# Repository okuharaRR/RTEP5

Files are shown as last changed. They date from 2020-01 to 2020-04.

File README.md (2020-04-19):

<p align="center">
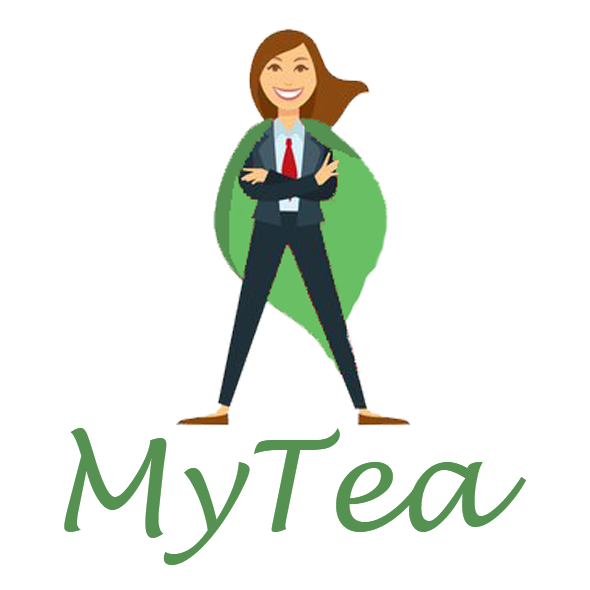
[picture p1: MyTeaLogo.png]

</p>

# MyTea - The perfect cuppa, every time

Welcome to the MyTea github page - the tea making machine which brings you the perfect tea experience!

_A Raspberry PI will be used to control the entire process of tea preparation. Depending on the tea chosen by the user, the system will heat up water to the required temperature, dispense the required amount of tea leaves into a filter, infuse the leaves for a specified time, and finally pour the tea into a cup._

_With so many coffee machines available to satisfy every variety of coffee that anyone has ever came up with, this product aims to deliver the ultimate tea experience in an office environment or a public institution so that tea drinkers are not left at the mercy of the primitive old kettle..._

## Installation

On the terminal of a Raspberry Pi type the following:

```git clone https://github.com/okuharaRR/RTEP5.git```

```cd TeaMaker```

```qmake```

```make```

```./TeaMaker```

[Qt](https://www.qt.io/download) and [WiringPi](http://wiringpi.com/) are required.

If ```make``` gives an error, try ```make clean``` first and ```make```.

## Using the application

Once a finished product is made, using it will be straightforward:

1. Fill up the kettle with water and make sure the switch in the back is in the ON position. (_The need for a mechanical switch is for user safety_.)
2. Fill up the dispenser with tea leaves.
3. Once done, turn on the RPI and launch the GUI application.
4. Follow the guide [here](https://github.com/okuharaRR/RTEP5/wiki/User-Manual).

That's it!

## Demonstration

_Covid-19 has caused a significant distruption of our project and a complete demonstartor cannot be built to date. More information about the impact of the outbreak can be found [here](https://github.com/okuharaRR/RTEP5/wiki/Impact-of-Covid-19)._

A demonstration of the current state of the project can be found [here](https://www.youtube.com/watch?v=PhV0StMdRJc).

## Team Structure
* Boris Yanchev
   * hardware design, implementation and testing
   * mechanical design, procurement and manufacturing
   * GUI conceptual design
   * marketing
* Mika Okuhara
   * software development and documentation
   * hardware and software integration
   * test GUI implementation
* Muhammad Adeel Akram
   * marketing

## Further links

For further information about our project, have a look at our [Wiki](https://github.com/okuharaRR/RTEP5/wiki).

For software documentation, please click [here](https://okuhararr.github.io/RTEP5/).

You can find our website [here](https://rtesps.wixsite.com/mytea). 

Also, be sure to like our [Facebook page](https://www.facebook.com/MyTea-%E8%8C%B6-114110590136382/) and follow our [Twitter](https://twitter.com/MyTea76121892) to get all the latest updates!

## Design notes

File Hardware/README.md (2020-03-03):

*** RTEP5 MyTea Hardware ReadMe File ***

Each subfolder contains the layout masks, schematics, and BOMs for each PCB used in the project.

The layout masks can be used directly for PCB fabrication. 

The interactive BOMs, when opened with an internet browser, can be used to see individual component placement and track the population of components.

Similarly, the text BOMs show all components used in text form.

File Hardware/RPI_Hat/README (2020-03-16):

This folder contains the KiCad files for the PI hat for connections to the rest of the sub-modules.

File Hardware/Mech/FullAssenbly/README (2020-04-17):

This folder contains the SOLIDWORKS models for the complete assembly.

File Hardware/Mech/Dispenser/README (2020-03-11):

SOLIDWORKS models for the tea dispenser can be found here.

Prototype dispenser built using 3mm laser-cut perspex sheets.

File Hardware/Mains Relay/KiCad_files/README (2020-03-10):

KiCad files for the sub-module are included here.

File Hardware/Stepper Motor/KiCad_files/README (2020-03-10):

KiCad files for the stepper motor sub-module can be found here.

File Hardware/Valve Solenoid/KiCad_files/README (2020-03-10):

KiCad files for the solenoid valve sub-module can be found here.

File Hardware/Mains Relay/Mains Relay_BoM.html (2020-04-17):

# C:\Users\Boris\Documents\KiCad Projects\RTEP5\Mains Relay\Mains Relay.sch

12.4.2020 г. 17:43:26

Eeschema (5.0.2)-1

Component Count:9

Ref | Qnty | Value | Part | Datasheet | Description | Vendor
C1 | 1 | 0.01u | Device:C | ~ | Unpolarized capacitor
D1 | 1 | Q_TRIAC_A1A2G | Device:Q_TRIAC_A1A2G | ~ | Triode for alternating current, anode1/anode2/gate
HS1 | 1 | Heatsink | Mechanical:Heatsink | | Heatsink
J1 | 1 | Conn_01x02_Male | Connector:Conn_01x02_Male | ~ | Generic connector, single row, 01x02, script generated (kicad-library-utils/schlib/autogen/connector/)
R2 | 1 | 120 | Device:R | ~ | Resistor
R3 | 1 | 360 | Device:R | ~ | Resistor
R4 | 1 | 330 | Device:R | ~ | Resistor
R5 | 1 | 39 | Device:R | ~ | Resistor
U1 | 1 | MOC3061M | Relay_SolidState:MOC3061M | http://www.fairchildsemi.com/ds/MO/MOC3061M.pdf | Zero Cross Opto-Triac, Vdrm 600V, Ift 15mA, DIP6

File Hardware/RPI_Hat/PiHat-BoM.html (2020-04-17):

# C:\Users\Boris\Documents\KiCad Projects\RTEP5\PiHat\PiHat.sch

12.4.2020 г. 18:15:18

Eeschema (5.0.2)-1

Component Count:9

Ref | Qnty | Value | Part | Datasheet | Description | Vendor
D1, D2 | 2 | LED | Device:LED | ~ | Light emitting diode
J1, J4 | 2 | Conn_01x03 | Connector_Generic:Conn_01x03 | ~ | Generic connector, single row, 01x03, script generated (kicad-library-utils/schlib/autogen/connector/)
J2 | 1 | Conn_01x04 | Connector_Generic:Conn_01x04 | ~ | Generic connector, single row, 01x04, script generated (kicad-library-utils/schlib/autogen/connector/)
J3 | 1 | Conn_02x20_Odd_Even | Connector_Generic:Conn_02x20_Odd_Even | ~ | Generic connector, double row, 02x20, odd/even pin numbering scheme (row 1 odd numbers, row 2 even numbers), script generated (kicad-library-utils/schlib/autogen/connector/)
J5 | 1 | Conn_01x02 | Connector_Generic:Conn_01x02 | ~ | Generic connector, single row, 01x02, script generated (kicad-library-utils/schlib/autogen/connector/)
R1, R2 | 2 | R | Device:R | ~ | Resistor

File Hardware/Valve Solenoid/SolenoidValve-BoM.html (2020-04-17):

# C:\Users\Boris\Documents\KiCad Projects\RTEP5\SolenoidValve\SolenoidValve.sch

12.4.2020 г. 18:19:06

Eeschema (5.0.2)-1

Component Count:12

Ref | Qnty | Value | Part | Datasheet | Description | Vendor
D1, D2 | 2 | D_Schottky | Device:D_Schottky | ~ | Schottky diode
J1 | 1 | Barrel_Jack | Connector:Barrel_Jack | ~ | DC Barrel Jack
J2, J3 | 2 | Conn_01x02 | Connector_Generic:Conn_01x02 | ~ | Generic connector, single row, 01x02, script generated (kicad-library-utils/schlib/autogen/connector/)
J4 | 1 | Conn_01x03 | Connector_Generic:Conn_01x03 | ~ | Generic connector, single row, 01x03, script generated (kicad-library-utils/schlib/autogen/connector/)
Q1, Q2 | 2 | Q_NMOS_GDS | Device:Q_NMOS_GDS | ~ | N-MOSFET transistor, gate/drain/source
R1, R3 | 2 | 1K | Device:R | ~ | Resistor
R2, R4 | 2 | 10K | Device:R | ~ | Resistor

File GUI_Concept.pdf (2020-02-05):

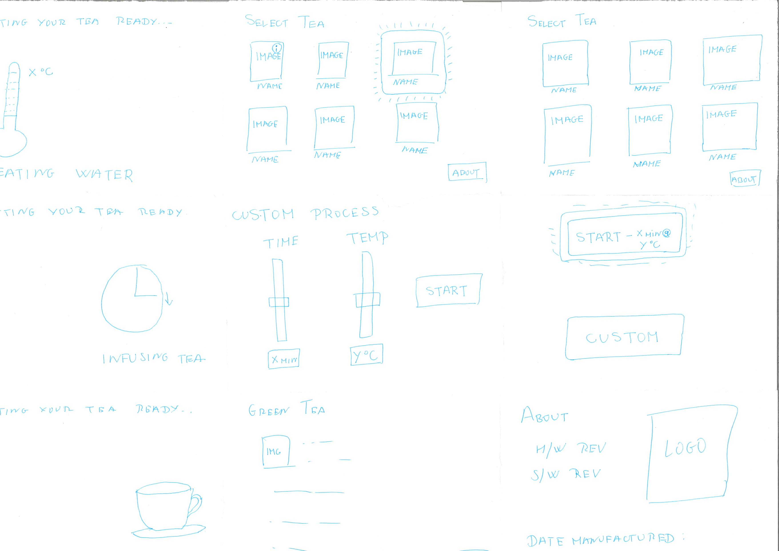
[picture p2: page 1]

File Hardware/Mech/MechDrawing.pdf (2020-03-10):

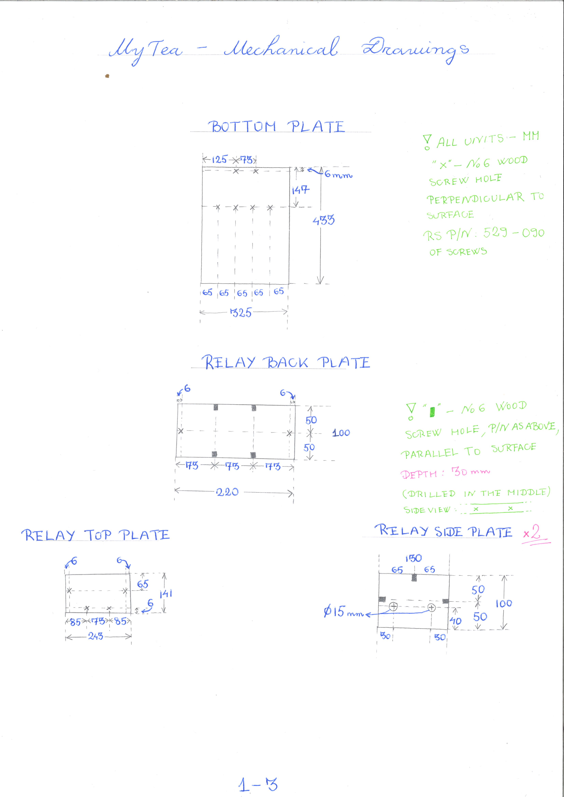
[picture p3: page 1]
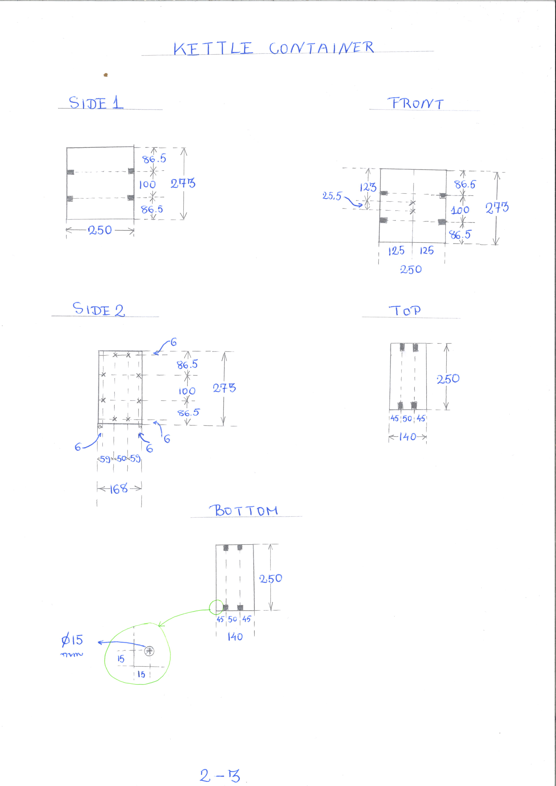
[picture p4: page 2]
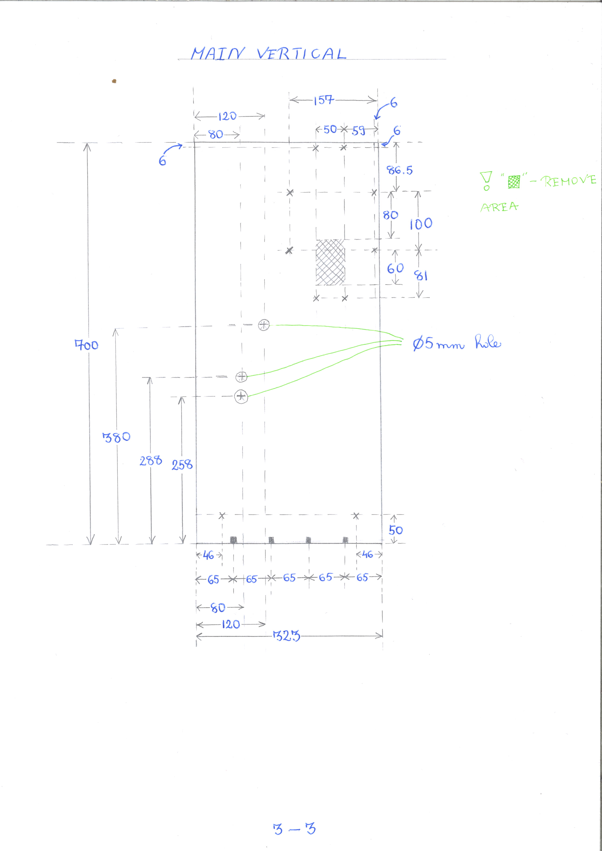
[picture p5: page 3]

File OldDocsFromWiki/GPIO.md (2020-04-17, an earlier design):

- [Blink LED](http://wiringpi.com/examples/blink/)
- [How to use GPIO](https://l.messenger.com/l.php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)
- [Turn on LED](https://l.messenger.com/l.phpu=https%3A%2F%2Fqiita.com%2Ftakanemu%2Fitems%2Fd3b9e3266c5041230b81&h=AT3YgtVzy_uaxKfw4oJJQ713obh4JMIo6F9qA105ZgJQhF4ASlV7CfIoCovFeMnMS9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)
- [Pin Number and locations](https://www.raspberrypi.org/documentation/usage/gpio/README.md)
- [Pin Allocations in WiringPi](http://wiringpi.com/pins/)

**WiringPi commands**

show manual: 
- man gpio 

Turn on and off LED:
- gpio -g mode 17 output 
- gpio -g write 17 1
- gpio -g write 17 0

Compile:
- make blink8

Execute:
- sudo ./blink8

Show PIN numbers:
- gpio readall

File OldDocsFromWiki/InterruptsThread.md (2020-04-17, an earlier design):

- [WiringPi](http://wiringpi.com/reference/priority-interrupts-and-threads/)
- [POSIX Thread 1](https://docs.oracle.com/cd/E19253-01/819-0390/tlib-12926/index.html)
- [POSIX Thread 2](https://computing.llnl.gov/tutorials/pthreads/)
- [Introduction to parallel computing](https://computing.llnl.gov/tutorials/parallel_comp/)

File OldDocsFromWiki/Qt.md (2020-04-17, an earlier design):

- [Installation](https://forum.qt.io/topic/105817/qt-creator-on-raspberry-pi4-4gb-ram/4)
- [Tutorial (Raspberry Pi + Qt + WiringPi)](https://www.youtube.com/watch?v=srgCRkyg5Zk)

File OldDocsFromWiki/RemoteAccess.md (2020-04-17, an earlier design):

(Enable ssh connection:
sudo raspi-config->window comes out)

Open terminal: Ctrl+Alt+T

Access server: 
ssh team20@rank510iot.eng.gla.ac.uk
Password: raspberry 

Access pi:
ssh -X pi@192.168.1.101
(See IP address: ifconfig)
( if pi is connected to same network, only this command is required)

Go to RETP5, ls, git status...

Security Settings:
- [Raspberry Pi Document](https://www.raspberrypi.org/documentation/configuration/security.md)
- [Initial Settings](https://l.messenger.com/l.php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)

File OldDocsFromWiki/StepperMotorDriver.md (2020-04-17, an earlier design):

- [DRV8825](https://uk.rs-online.com/web/p/motor-driver-ics/7422873/)
- [DATASHEET](http://www.ti.com/lit/ds/symlink/drv8825.pdf)
- [Sample C++ code](https://crish4cks.net/a-simple-c-library-to-drive-a-stepper-motor-using-the-raspberry-pi/)
- [Tutorial 1](https://l.messenger.com/l.php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)
- [Tutorial 2](https://l.messenger.com/l.php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)
- [Tutorial 3](https://l.messenger.com/l.php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)

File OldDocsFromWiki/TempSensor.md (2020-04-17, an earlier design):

- water temperature for tea brewing 75-100 deg C: [Source 1](https://lifehacker.com/this-time-and-temperature-chart-helps-you-brew-the-perf-1447451469), [Source 2](http://www.sayteaonbloor.com/tea101.html)

- digital, submersible sensor preferred

-> DS18B20 waterproof sensor chosen:
- 750ms sampling time
- 0.5 deg C -> 0.0625 deg C accuracy
- threshold mode
- digital, online example [EXAMPLE](http://www.circuitbasics.com/raspberry-pi-ds18b20-temperature-sensor-tutorial/)
- cost: ~£5 from Amazon [LINK](https://www.amazon.co.uk/DS18B20-Waterproof-Temperature-Transducer-Raspberry-Yellow/dp/B01MY9QR49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), eBay [LINK](https://www.ebay.co.uk/itm/1-2-5-10-DS18B20-Waterproof-Sensor-Digital-thermometer-Probe-With-PARASITE-MODE/262546255984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), RS [LINK](https://uk.rs-online.com/web/c/semiconductors/sensor-ics/temperature-sensors-humidity-sensors/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), [MOUSER](https://www.mouser.co.uk/Search/Refine?Keyword=DS18B20&FS=True)

Resources:
[Datasheet](https://datasheets.maximintegrated.com/en/ds/DS18B20.pdf), [1-Wire Setting (Japanese)](https://deviceplus.jp/hobby/raspberrypi_entry_018/), [C++ Example](https://www.iot-programmer.com/index.php/books/22-raspberry-pi-and-the-iot-in-c/chapters-raspberry-pi-and-the-iot-in-c/38-raspberry-pi-and-the-iot-in-c-ds18b20-tempe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), [ANOTHER EXAMPLE](http://bradsrpi.blogspot.com/2013/12/c-program-to-read-temperature-from-1.html), [AND ANOTHER ONE](https://www.sunfounder.com/learn/sensor-kit-v2-0-for-raspberry-pi-b-plus/lesson-26-ds18b20-temperature-sensor-sensor-kit-v2-0-for-b-plus.html), [DATASHEET WITH EXAMPLE](https://media.digikey.com/pdf/Data%20Sheets/DFRobot%20PDFs/DFR0198_Web.pdf)

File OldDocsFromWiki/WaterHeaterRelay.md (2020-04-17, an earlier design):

Flow of liquids from a container calculation:
[LINK](https://www.engineeringtoolbox.com/flow-liquid-water-tank-d_1753.html)

Standard size tea cup?
- various sources: 170ml, 150ml
- Japanese yunomi: 90-160ml

Want container to be enough for at least two cups

A commercial kettle will be used to heat the water which will be dispensed via a pipe connecting to the bottom of the kettle.

Advantages:
- cheaper (~£10 for kettle)
- kettle and container in one package
- researched immersion heaters are either expensive (mains) or cheap and of questionable quality (portable DC ones)

Disadvantages:
- mains-powered design
- not very elegant
- more difficult to estimate amount of water dispensed

Parts:
- any kettle - [AMAZON LINK](https://www.amazon.co.uk/Daewoo-SDA1683GE-Protection-1850-2200W-Power-Cream/dp/B07RQLKHCR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)
- relay board (or designed) [LINK](https://uk.rs-online.com/web/p/power-management-development-kits/8430834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)

- [EXAMPLE RELAY](https://cdn-shop.adafruit.com/product-files/268/268_instructionsheet.pdf)

Parts list:
- [MOC3061](https://uk.rs-online.com/web/p/optocoupler-ics/6711440/) 2.9
- [BTA26](https://uk.rs-online.com/web/p/triacs/7140515/) 3.04
- [390Ohm 1W](https://uk.rs-online.com/web/p/through-hole-fixed-resistors/2141074/) 0.67
- [39Ohm 1W](https://uk.rs-online.com/web/p/through-hole-fixed-resistors/2140958/) 0.21
- [4K/W heatsink](https://uk.rs-online.com/web/p/heatsinks/1898151/) 3.03
- [Safety Capacitors .01uF 480Vac 20%](https://www.mouser.co.uk/ProductDetail/Vishay-BC-Components/F339X131048MFP2B0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) 0.286

Misc:
- [connectors](https://uk.rs-online.com/web/p/hose-connectors/5067200/)
- [tubing](https://www.amazon.co.uk/10mm-13mm-Clear-Unreinforced-Tubing/dp/B00ABXC9YQ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)

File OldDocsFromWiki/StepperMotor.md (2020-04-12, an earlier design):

Stepper motor:

- [TUTORIAL](https://www.youtube.com/watch?v=LUbhPKBL_IU)

- [LESSON](https://learn.adafruit.com/adafruits-raspberry-pi-lesson-10-stepper-motors/overview)

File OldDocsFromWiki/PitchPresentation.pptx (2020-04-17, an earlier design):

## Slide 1

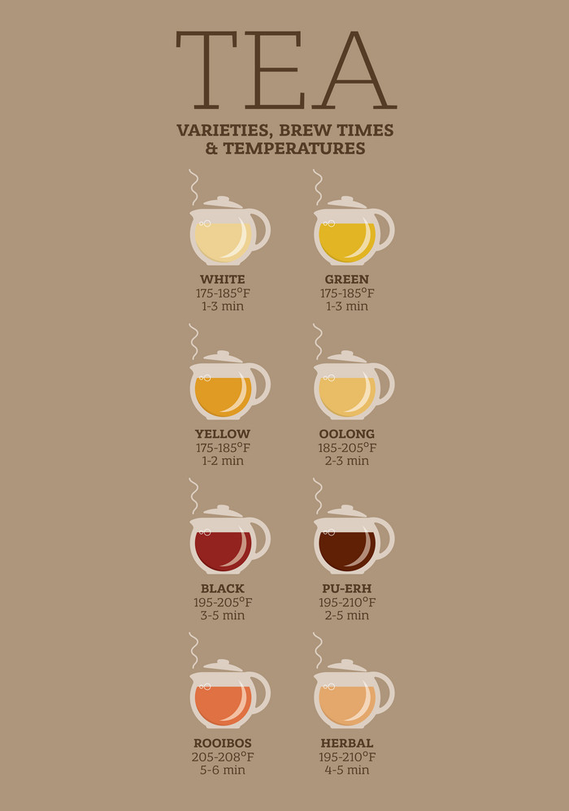
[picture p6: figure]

https://www.vectorstock.com/royalty-free-vector/tea-varieties-brewing-time-and-temperature-vector-10972987

- 85% of British population drink tea daily¹
- 100 million cups daily, coffee – 70 million¹
- 96% - teabag¹…
- specific brew time and temp. depending on tea
- tea and water amount also important

¹ - FAQ's about Tea, UK Tea and Infusions Association

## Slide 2

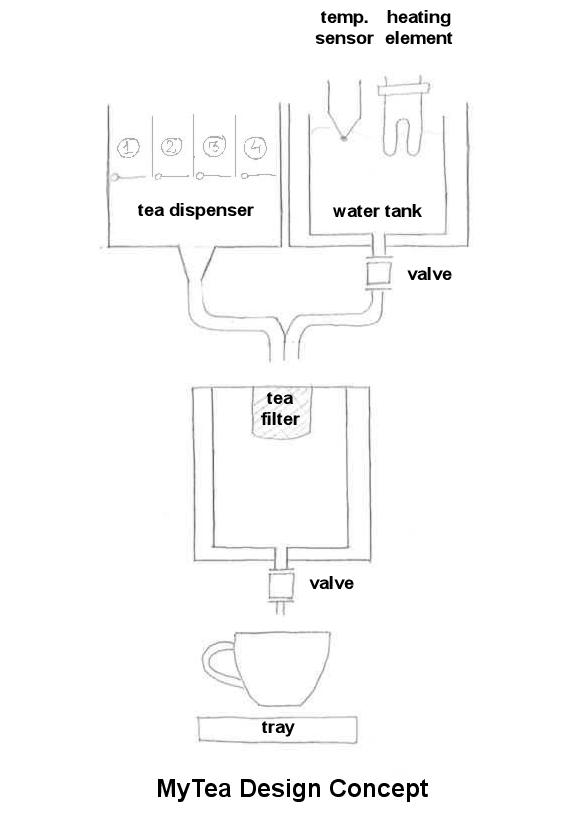
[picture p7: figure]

The main idea:

- desired tea selected via GUI
- control water temperature
- pour exact amount of water
- dispense exact amount of leaves
- infuse and dispense tea

Potential extras:

completely customisable preparation

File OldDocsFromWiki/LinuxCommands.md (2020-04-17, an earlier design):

- touch: make a file 
- nano: edit file 
- g++ -o test test.cpp: compile test.cpp
- ./test: execute compiled file (test)
- cd /: go to home 
- sudo apt-get update: update the pi 
- sudo halt: shut down  
- pwd: see directory path

- apt-catch search: search for software
- apt-cache show: show software information 
- df: show available disk space 
- wget: download a file from the web

- grep: search certain patterns in a file
- awk: search text files
- find: search directories 
- whereis: find location of command 

- ping: check if communication can be made with another host 
- nmap: network exploration & scanning 
- hostname: display current hostname
- ifconfig: display network configuration details for interfaces 

Compile multiple files:
- cmake: make a list of code
- make: compile 

Execute: ./blink

**Git Commands**

- show commands: git 

- Update git: sudo apt-get install git 

- Copy repository: git clone http://github.com/okuharaRR/RTEP5.git

go to RETP5 directory
- Make changes to files: ex. nano test.txt

- See the status: git status
- Add the change: git add README.md
- (git status)

Commit:
- git config - - global user.email “okuhara.sotsuken@gmail.com”

- git config - - global user.name “okuharaRR”

- git commit -m “this is my first commit”

- (git status)

Push: git push

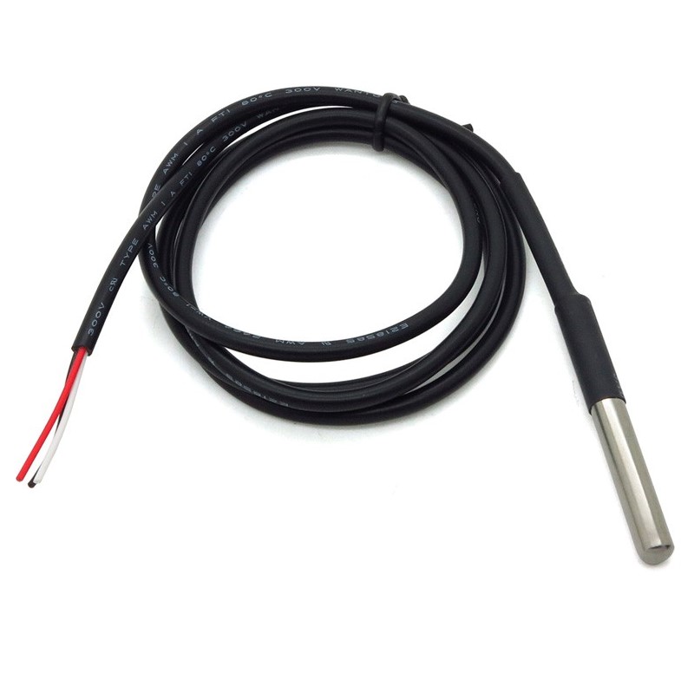
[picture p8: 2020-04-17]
Hardware/Images/DS18B20.jpg

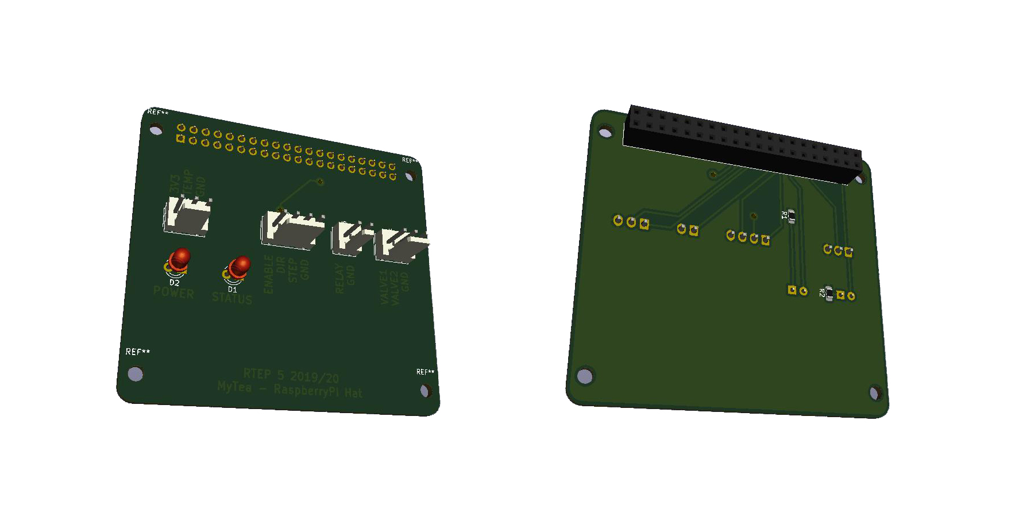
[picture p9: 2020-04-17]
Hardware/Images/PiHat.jpg

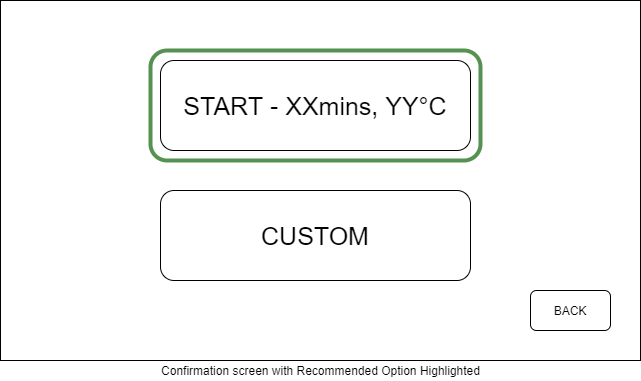
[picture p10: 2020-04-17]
Software/GUI_Concept/5-ConfScreen.png

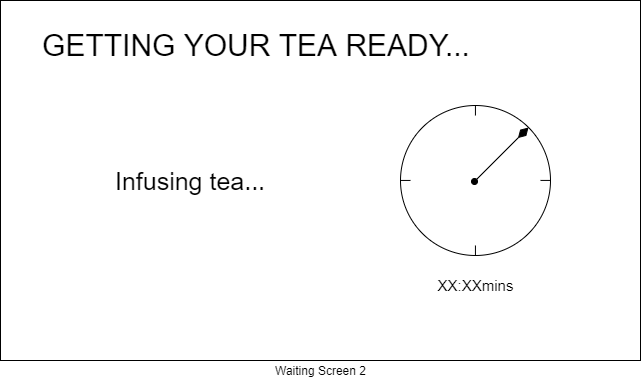
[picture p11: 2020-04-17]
Software/GUI_Concept/8-Wait2.png

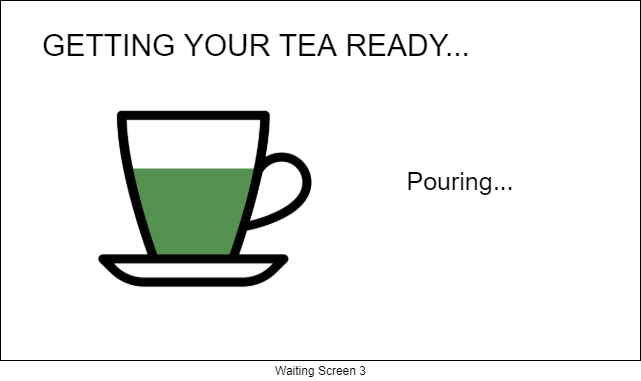
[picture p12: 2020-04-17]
Software/GUI_Concept/9-Wait3.png

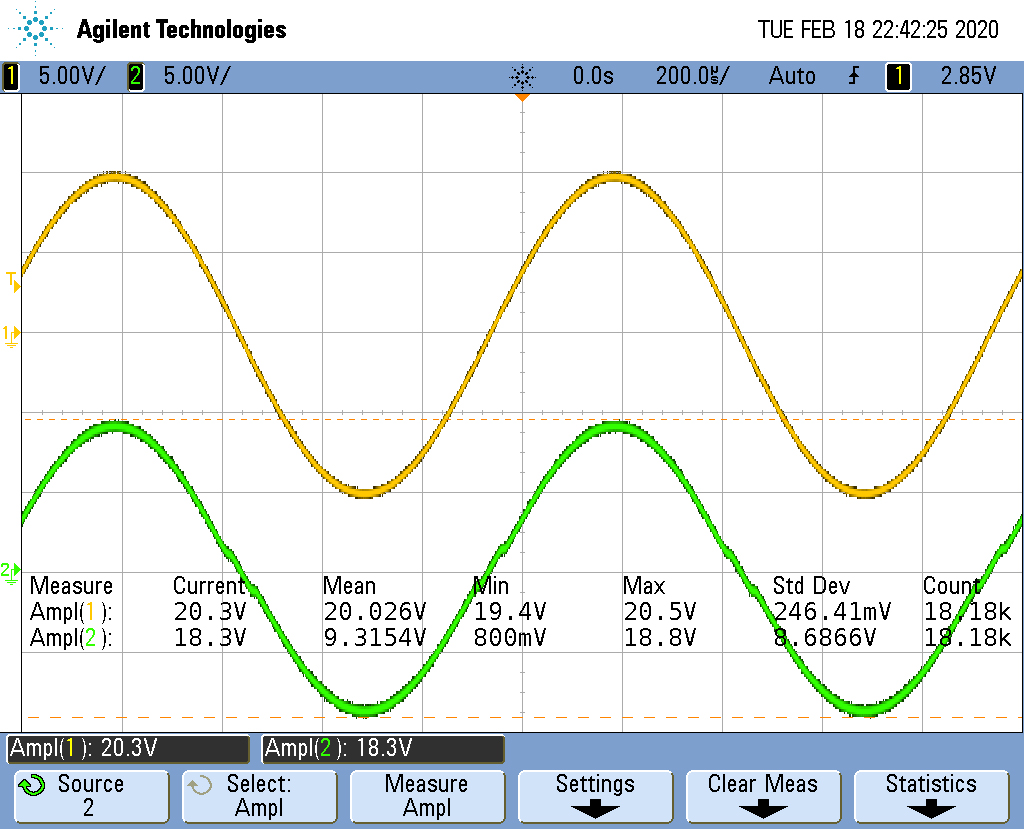
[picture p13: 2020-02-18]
Hardware/Mains Relay/Mains_ControlOn.jpg

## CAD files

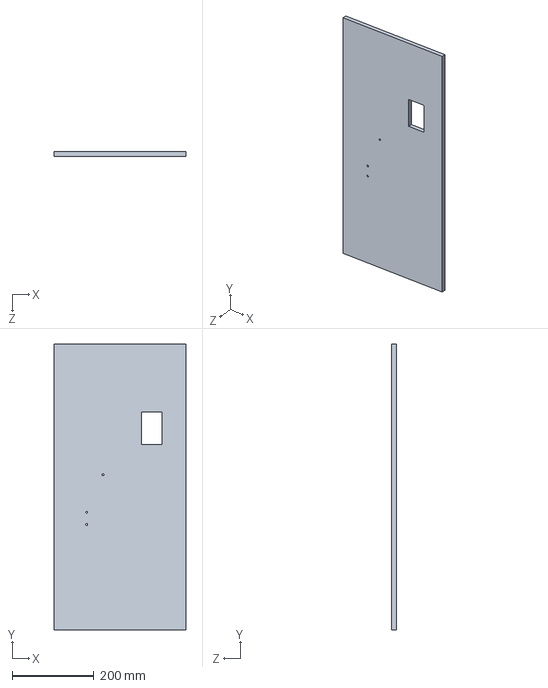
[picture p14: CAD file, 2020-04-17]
Hardware/Mech/FullAssenbly/MainVertical.SLDPRT
323.0 x 700.0 x 11.5 mm

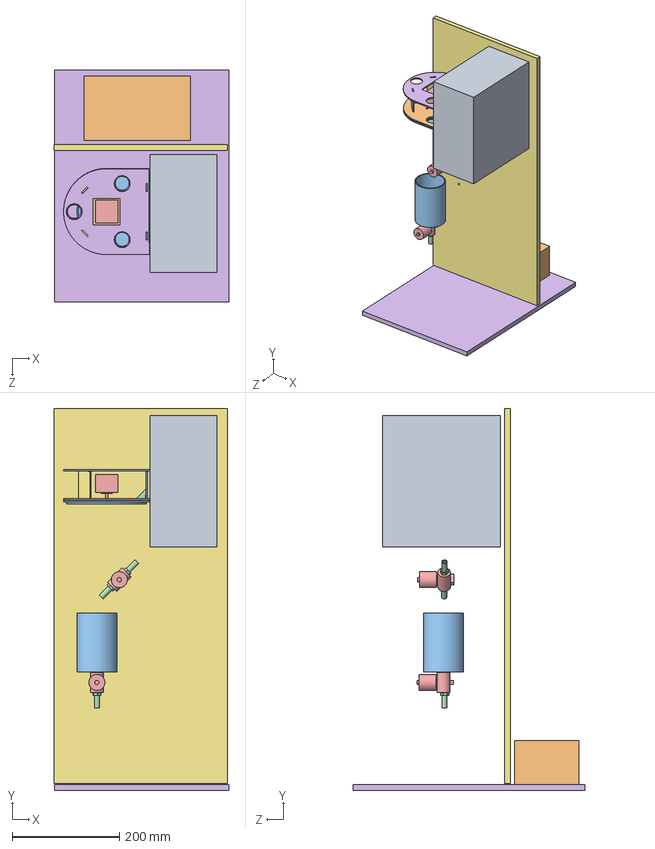
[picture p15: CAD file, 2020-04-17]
Hardware/Mech/FullAssenbly/TestAssembly.SLDASM
325.7 x 712.7 x 433.0 mm
BottomPlate13mm
BottomPlate15mm
BottomPlateRot
L_Conn x 4
StepperMotor
TopPlate
VerticalPlateNoHole x 2
VerticalPlate x 2
KettleBox
RelayBox
Container
Fitting x 3
Valve x 2
BasePlate
MainVertical

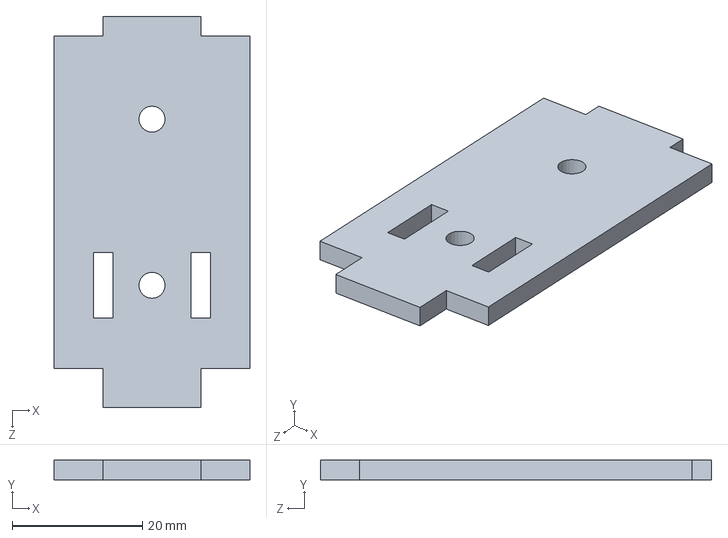
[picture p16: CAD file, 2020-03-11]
Hardware/Mech/Dispenser/VerticalPlate.SLDPRT
30.0 x 3.00 x 60.0 mm

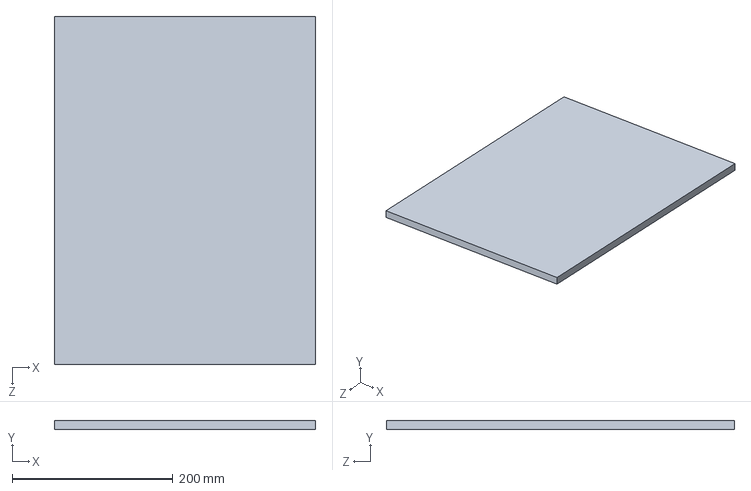
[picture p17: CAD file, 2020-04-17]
Hardware/Mech/FullAssenbly/BasePlate.SLDPRT
325.0 x 11.5 x 433.0 mm

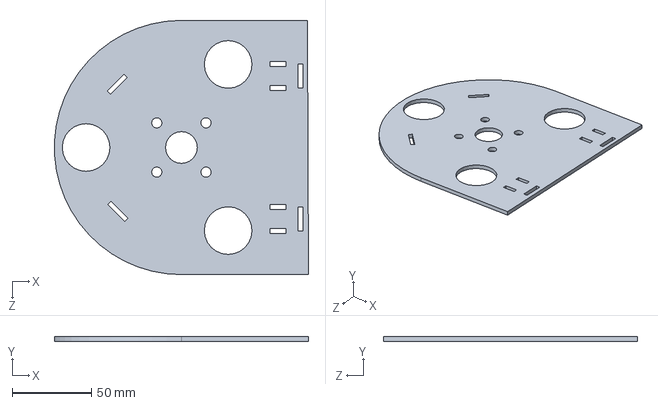
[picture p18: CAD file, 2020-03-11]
Hardware/Mech/Dispenser/BottomPlate15mm.SLDPRT
159.9 x 3.00 x 160.0 mm

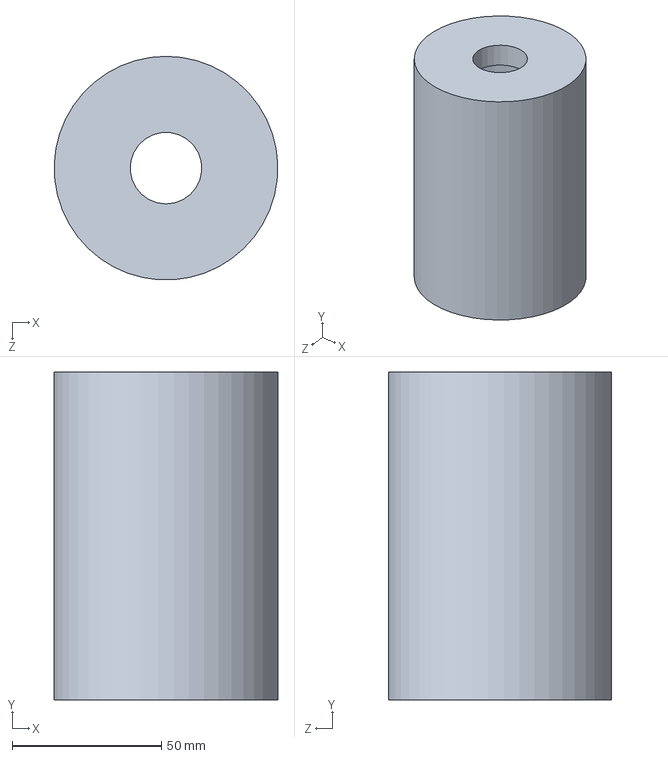
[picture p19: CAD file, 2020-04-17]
Hardware/Mech/FullAssenbly/Container.SLDPRT
75.0 x 110.0 x 74.9 mm

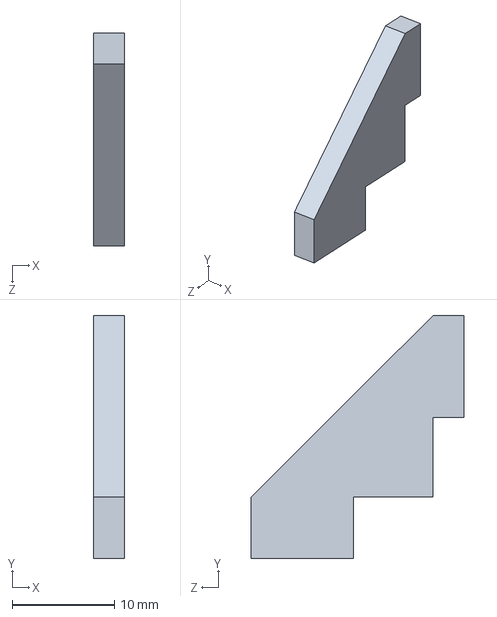
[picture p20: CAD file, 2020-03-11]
Hardware/Mech/Dispenser/L_Conn.SLDPRT
3.00 x 23.7 x 20.8 mm

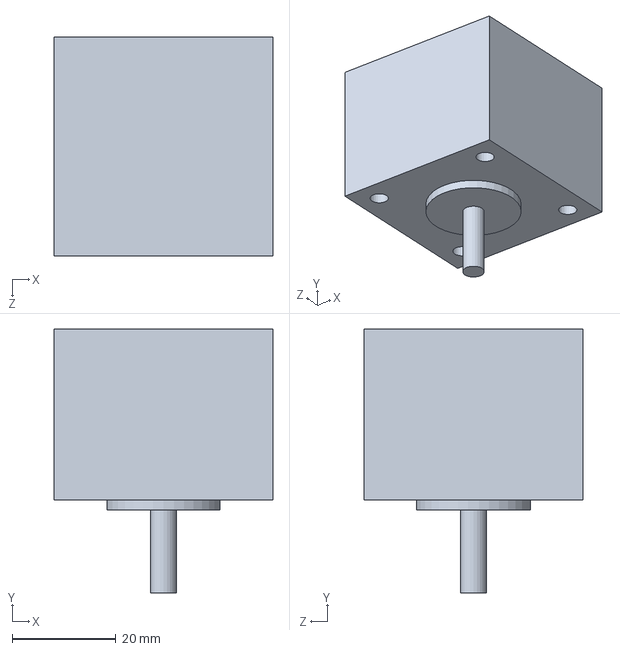
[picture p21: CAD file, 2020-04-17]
Hardware/Mech/FullAssenbly/StepperMotor.SLDPRT
42.3 x 51.0 x 42.3 mm

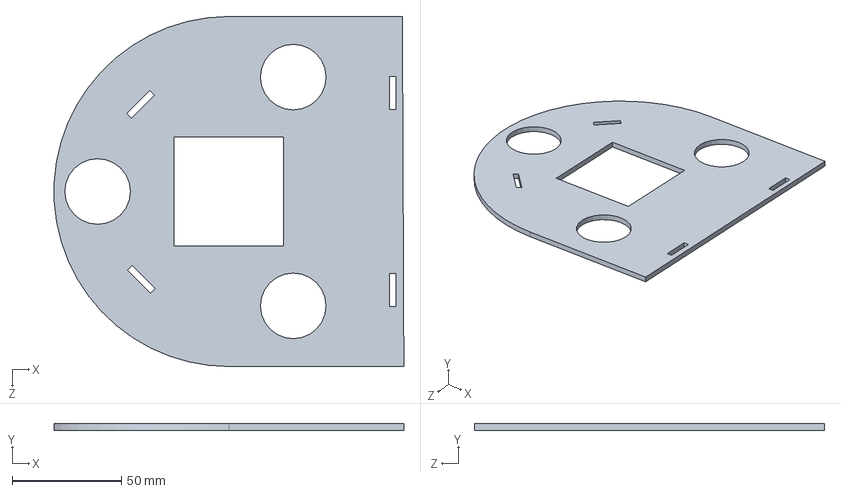
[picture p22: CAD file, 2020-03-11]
Hardware/Mech/Dispenser/TopPlate.SLDPRT
159.9 x 3.00 x 160.0 mm

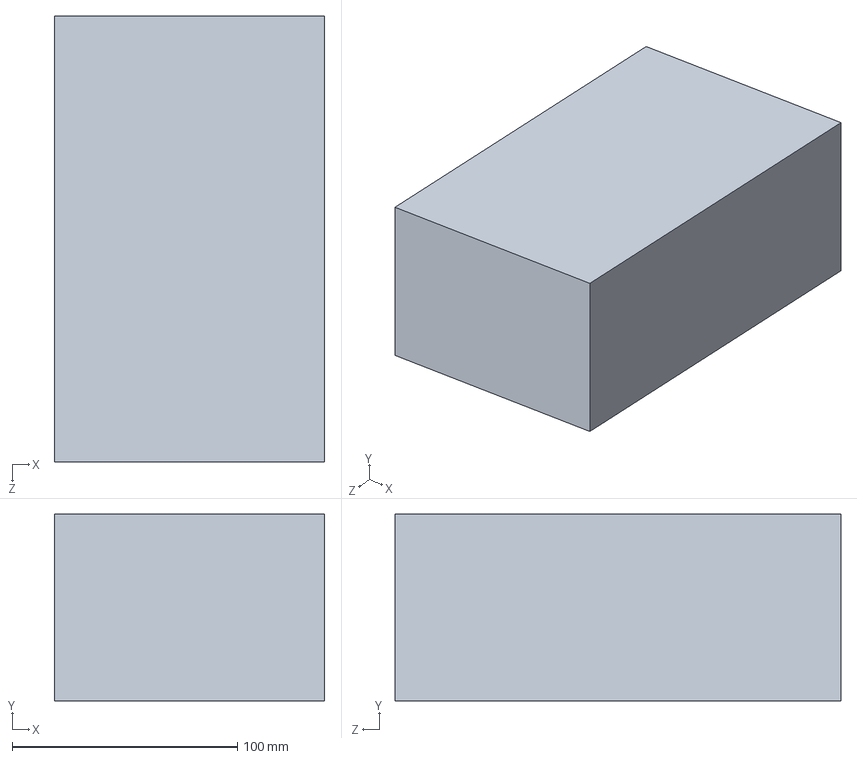
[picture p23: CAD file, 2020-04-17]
Hardware/Mech/FullAssenbly/RelayBox.SLDPRT
120.0 x 83.0 x 198.0 mm

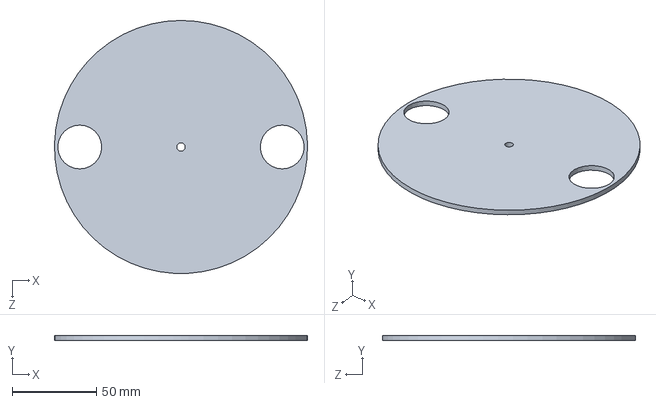
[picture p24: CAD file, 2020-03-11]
Hardware/Mech/Dispenser/BottomPlateRot.SLDPRT
149.9 x 3.00 x 150.0 mm

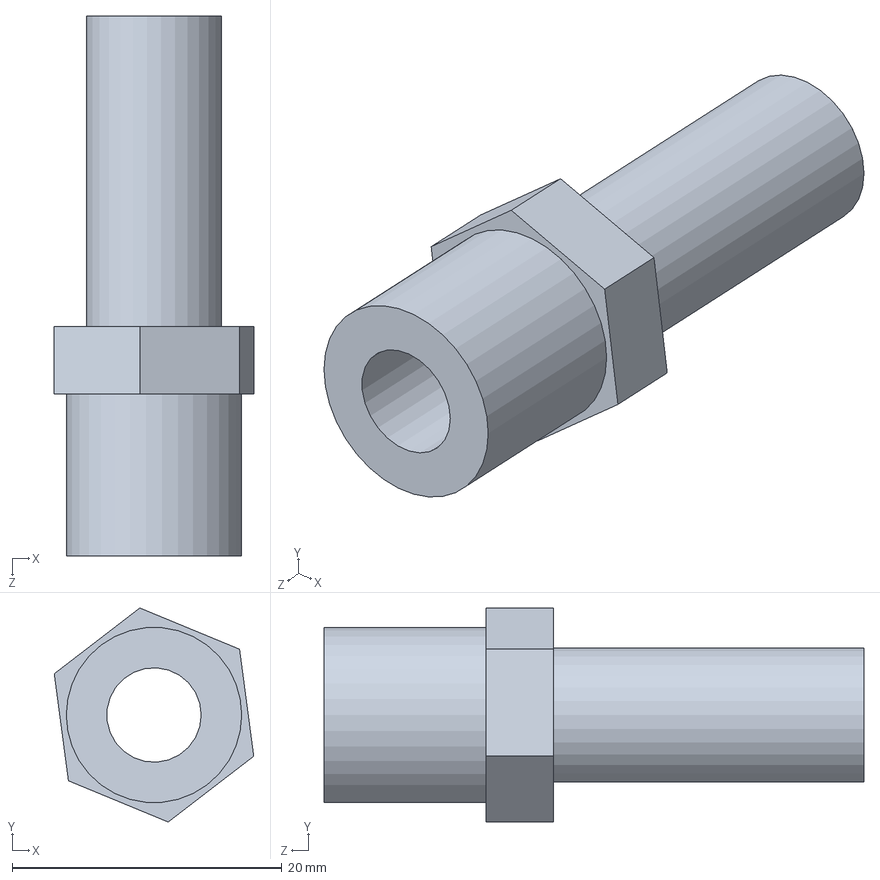
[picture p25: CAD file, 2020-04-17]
Hardware/Mech/FullAssenbly/Fitting.SLDPRT
14.8 x 15.9 x 40.0 mm

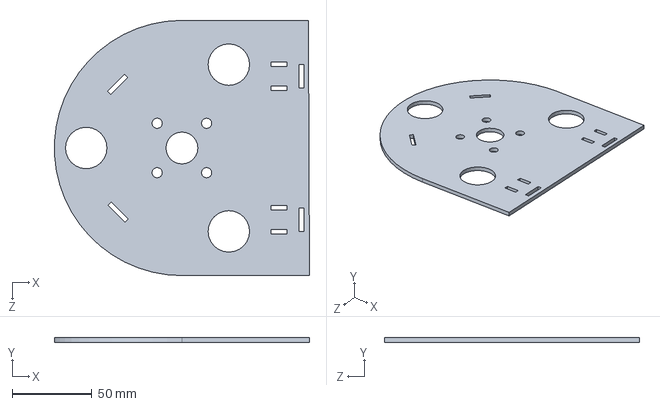
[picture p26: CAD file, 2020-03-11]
Hardware/Mech/Dispenser/BottomPlate13mm.SLDPRT
159.9 x 3.00 x 160.0 mm

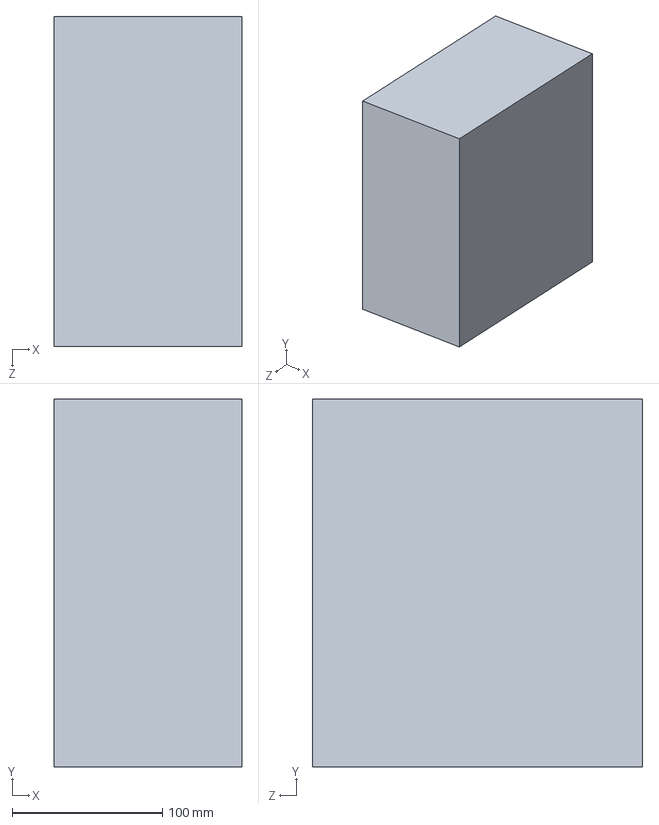
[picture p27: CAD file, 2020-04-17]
Hardware/Mech/FullAssenbly/KettleBox.SLDPRT
125.0 x 245.0 x 220.0 mm

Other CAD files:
Hardware/Mech/Dispenser/VerticalPlateNoHole.SLDPRT
Hardware/Mech/FullAssenbly/Valve.SLDPRT

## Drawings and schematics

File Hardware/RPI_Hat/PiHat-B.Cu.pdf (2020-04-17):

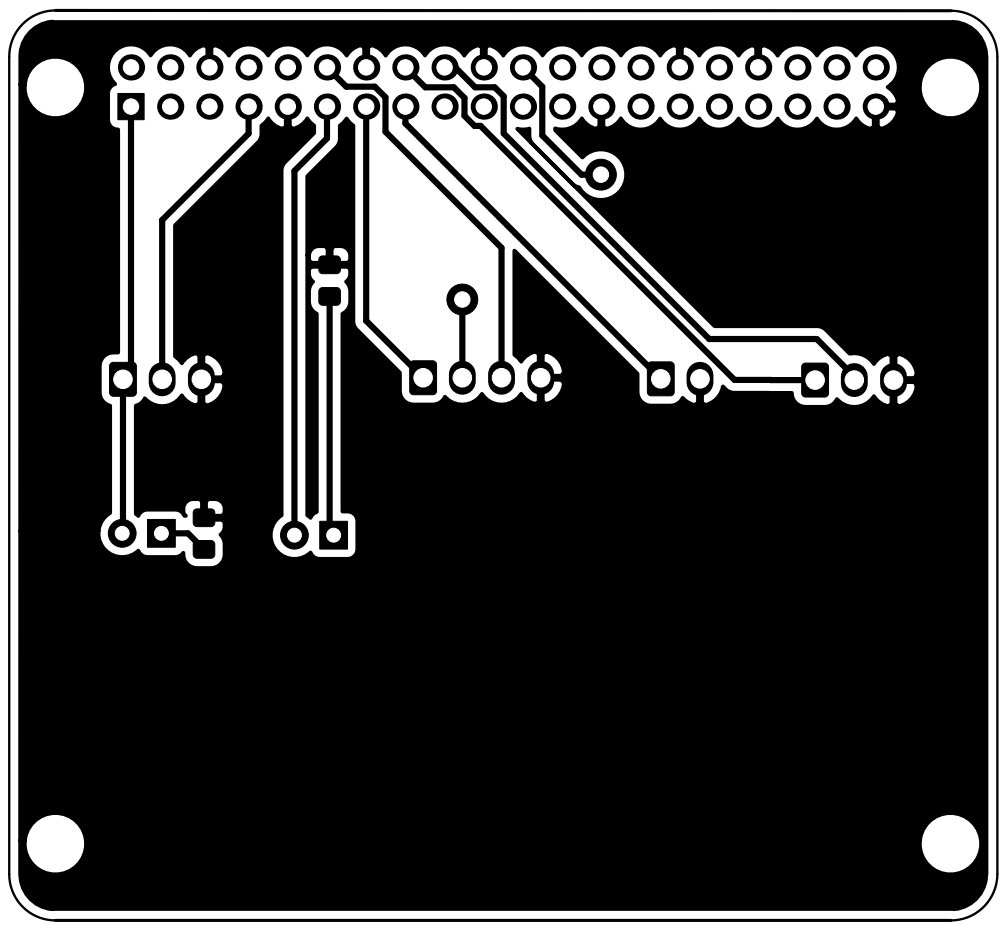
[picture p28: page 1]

Drawn by Boris Yanchev
File: PiHat.kicad_pcb Sheet: Real Time Embedded Programming 5 2019/20

Id: 1/1 Title: MyTea - RaspberryPI Hat

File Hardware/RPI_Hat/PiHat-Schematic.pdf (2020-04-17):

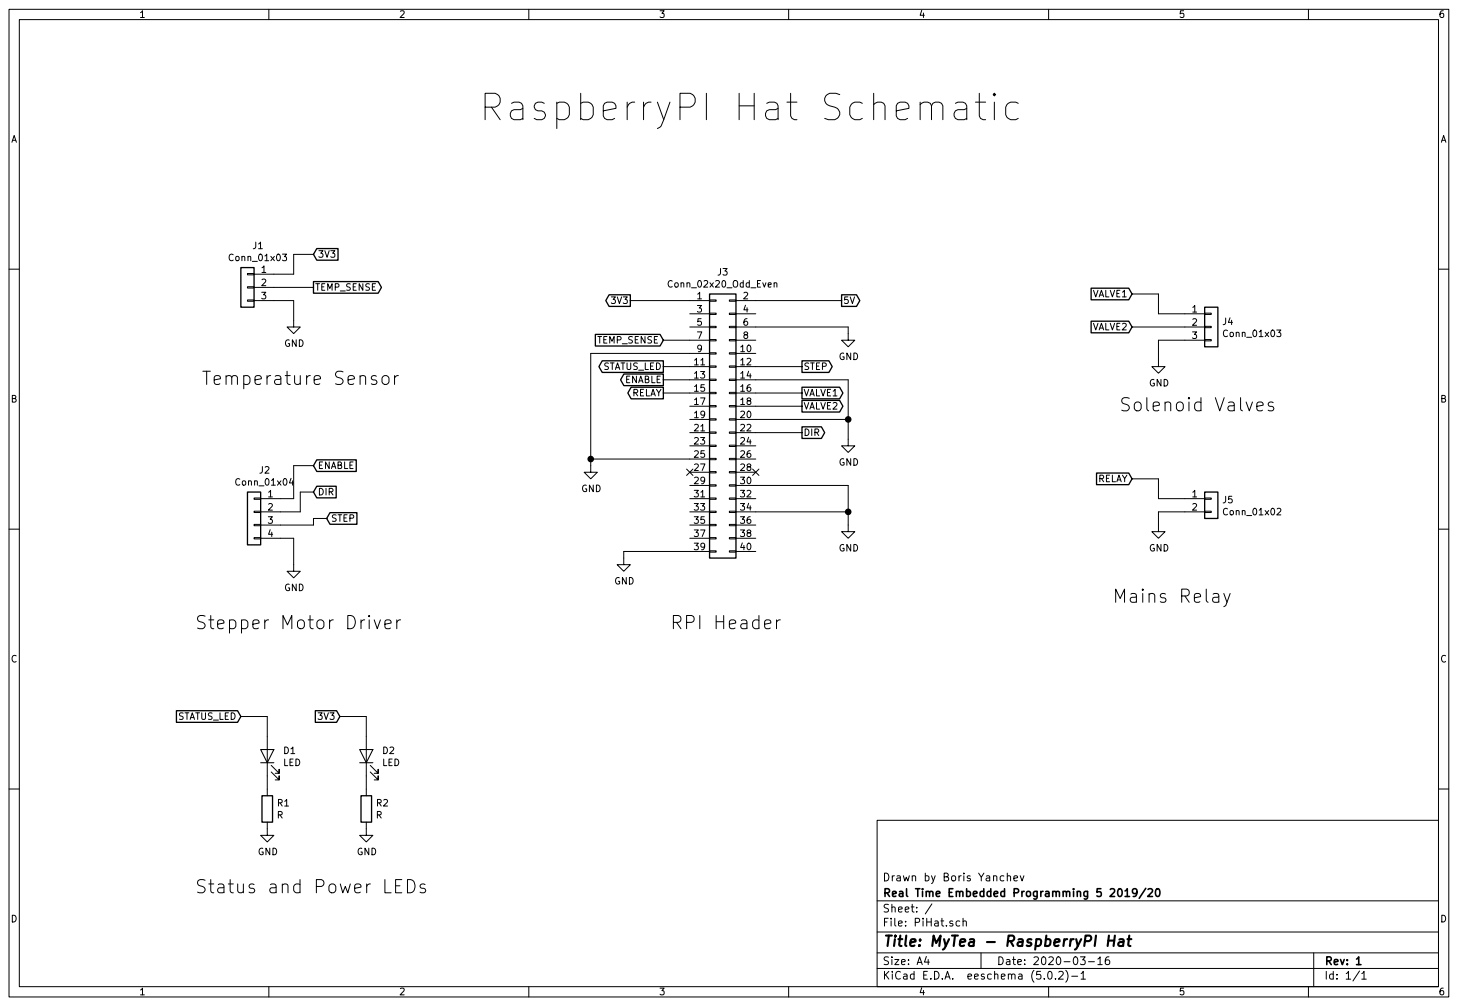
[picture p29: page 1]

ENABLE Stepper Motor Driver

Drawn by Boris Yanchev
Id: 1/1 Title: MyTea - RaspberryPI Hat File: PiHat.sch Sheet: / Real Time Embedded Programming 5 2019/20

Status and Power LEDs

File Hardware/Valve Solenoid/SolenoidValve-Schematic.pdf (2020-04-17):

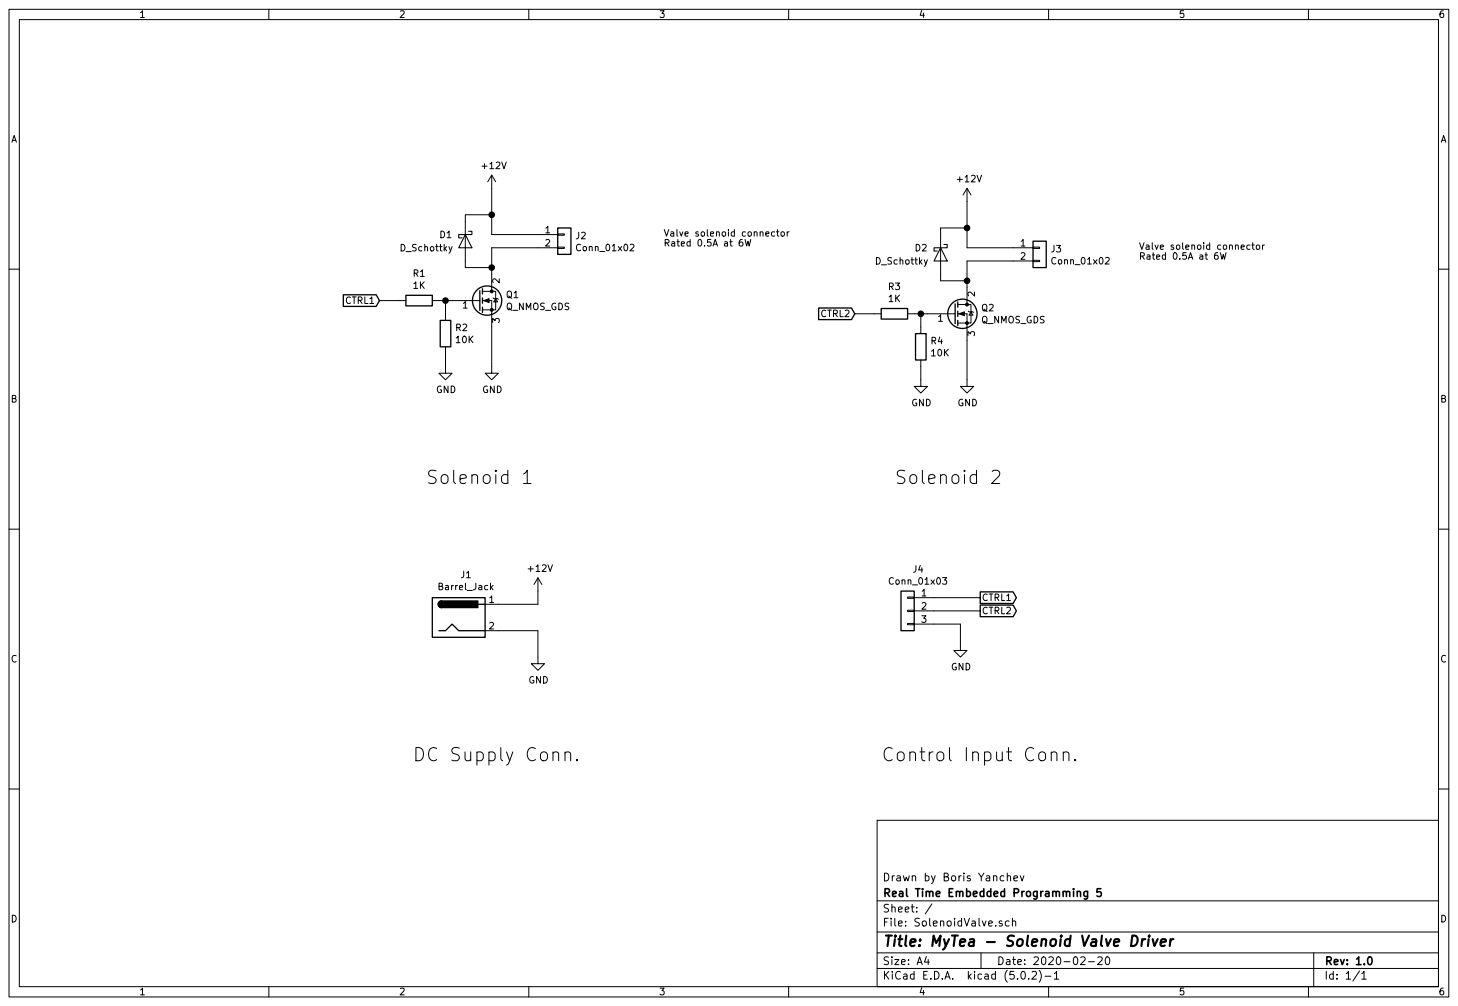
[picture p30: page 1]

Drawn by Boris Yanchev
Id: 1/1 Title: MyTea - Solenoid Valve Driver File: SolenoidValve.sch Sheet: / Real Time Embedded Programming 5

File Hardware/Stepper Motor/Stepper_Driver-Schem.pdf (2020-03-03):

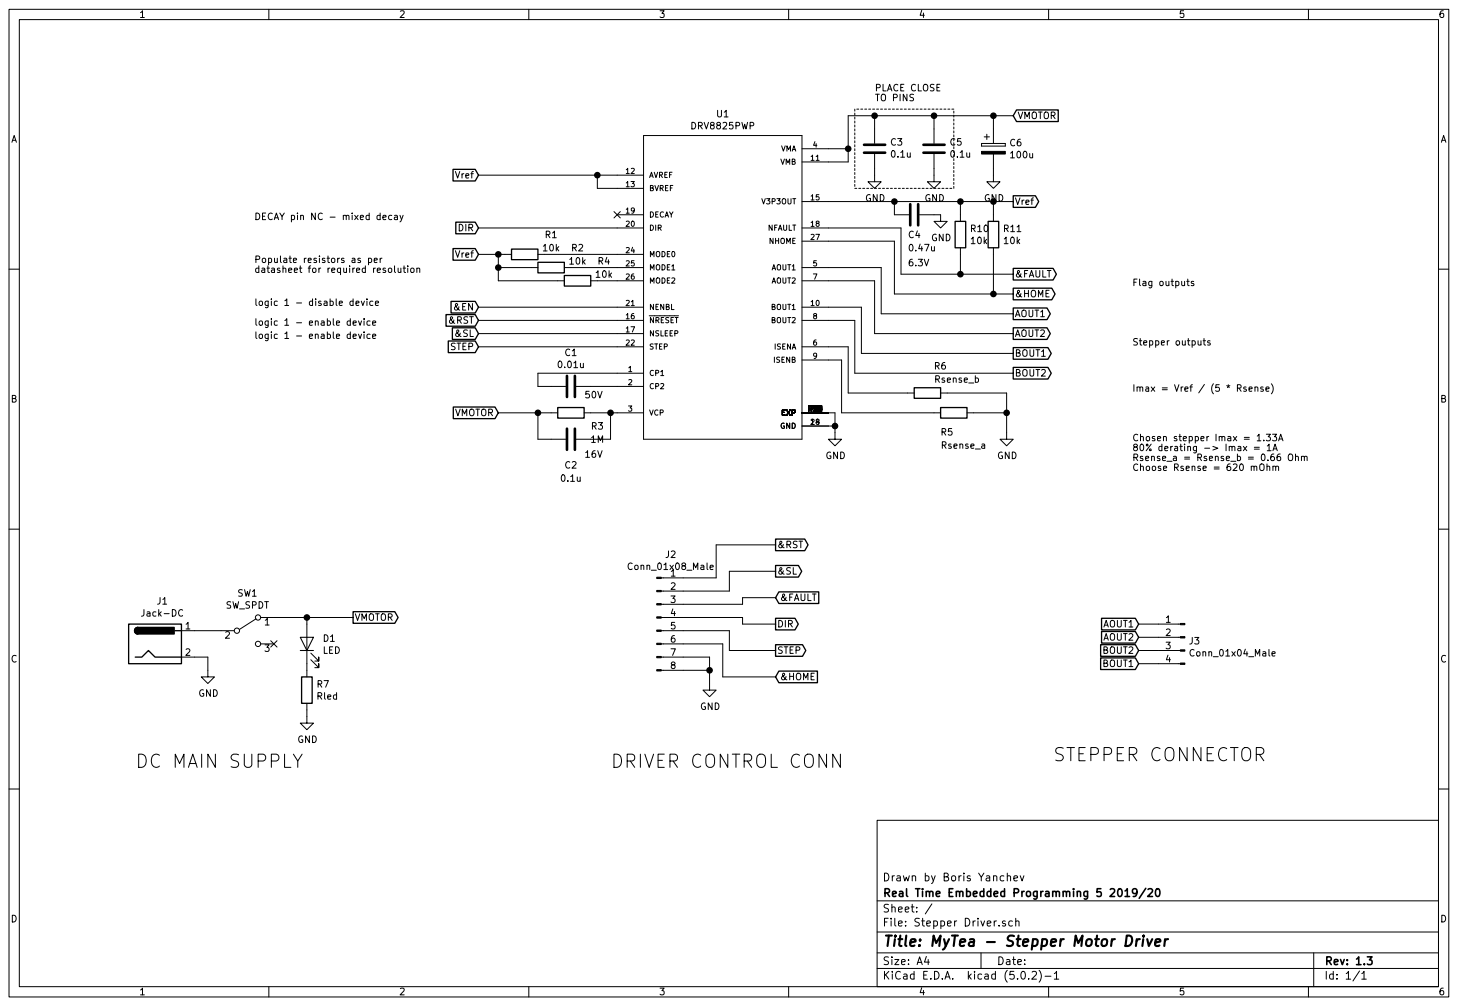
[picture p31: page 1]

10k DECAY pin NC - mixed decay

10k Populate resistors as per

VMOTOR DC MAIN SUPPLY

Drawn by Boris Yanchev
File: Stepper Driver.sch Sheet: / Real Time Embedded Programming 5 2019/20

Id: 1/1 Title: MyTea - Stepper Motor Driver

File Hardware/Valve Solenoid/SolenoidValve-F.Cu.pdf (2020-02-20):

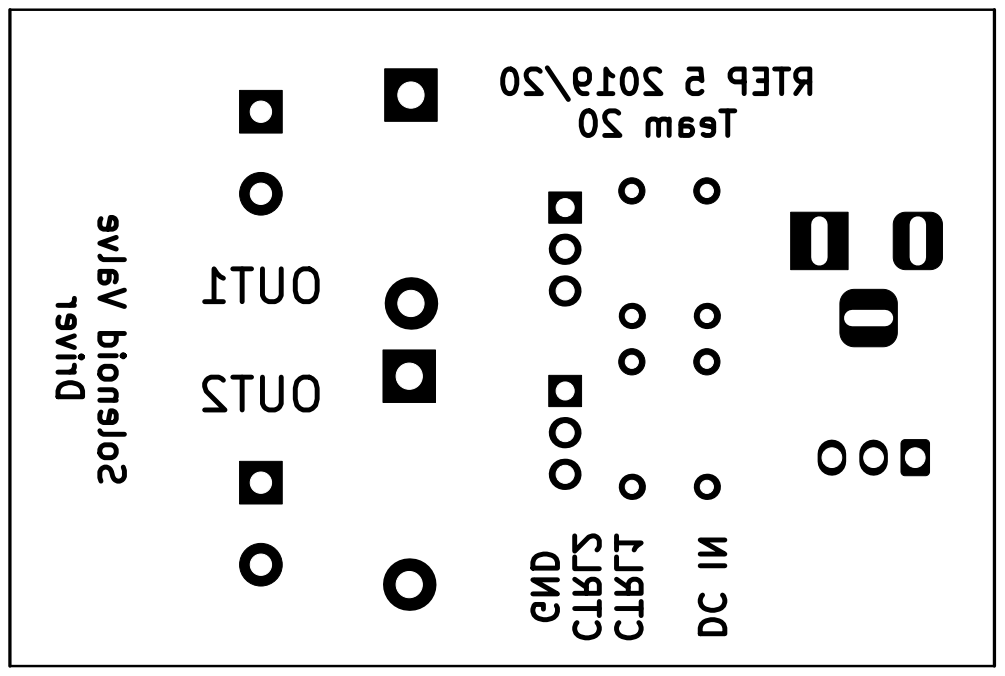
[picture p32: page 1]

GND CTRL2 CTRL1 DC IN Solenoid Valve Driver RTEP 5 2019/20 Team 20 OUT1

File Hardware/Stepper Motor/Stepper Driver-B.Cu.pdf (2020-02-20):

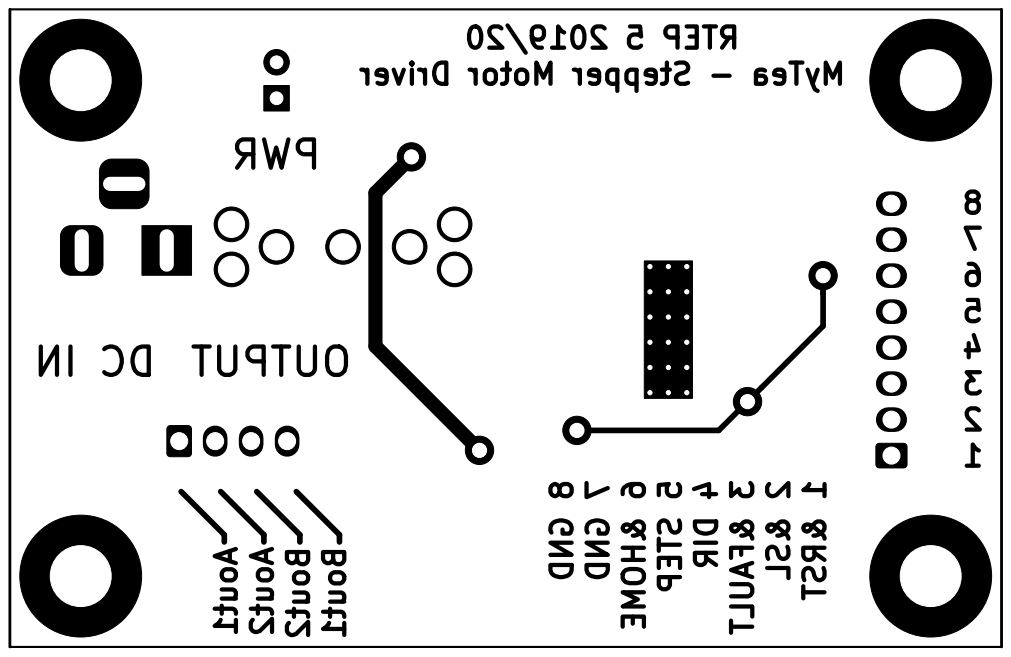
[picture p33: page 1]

RTEP 5 2019/20 MyTea - Stepper Motor Driver 8

1 8 GND 7 GND 6 &HOME 5 STEP 4 DIR 3 &FAULT 2 &SL 1 &RSTAout1 Aout2 Bout2 Bout1

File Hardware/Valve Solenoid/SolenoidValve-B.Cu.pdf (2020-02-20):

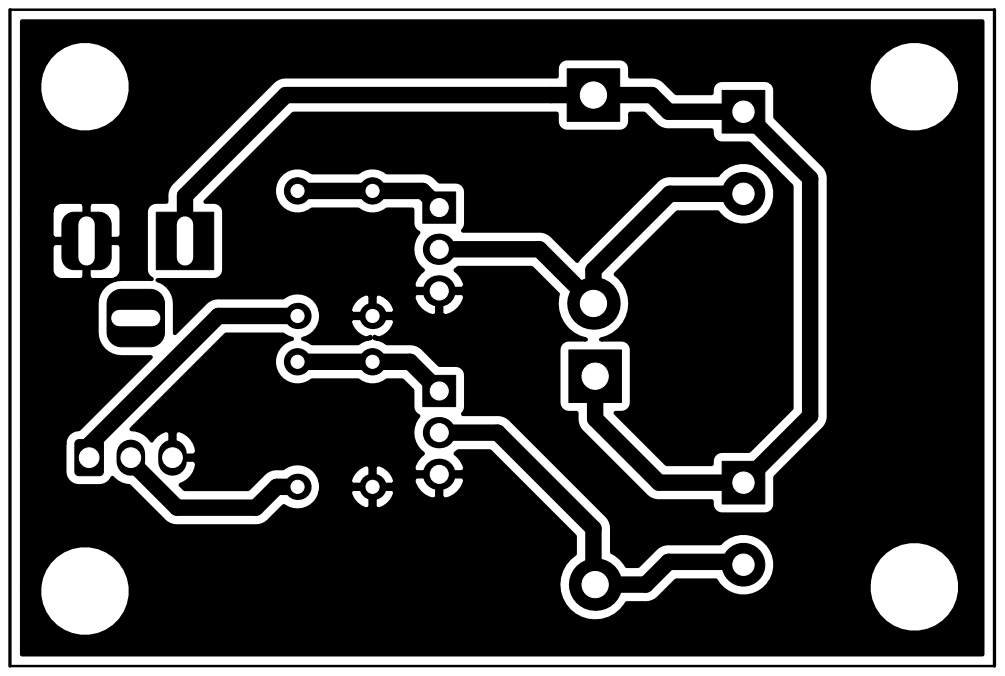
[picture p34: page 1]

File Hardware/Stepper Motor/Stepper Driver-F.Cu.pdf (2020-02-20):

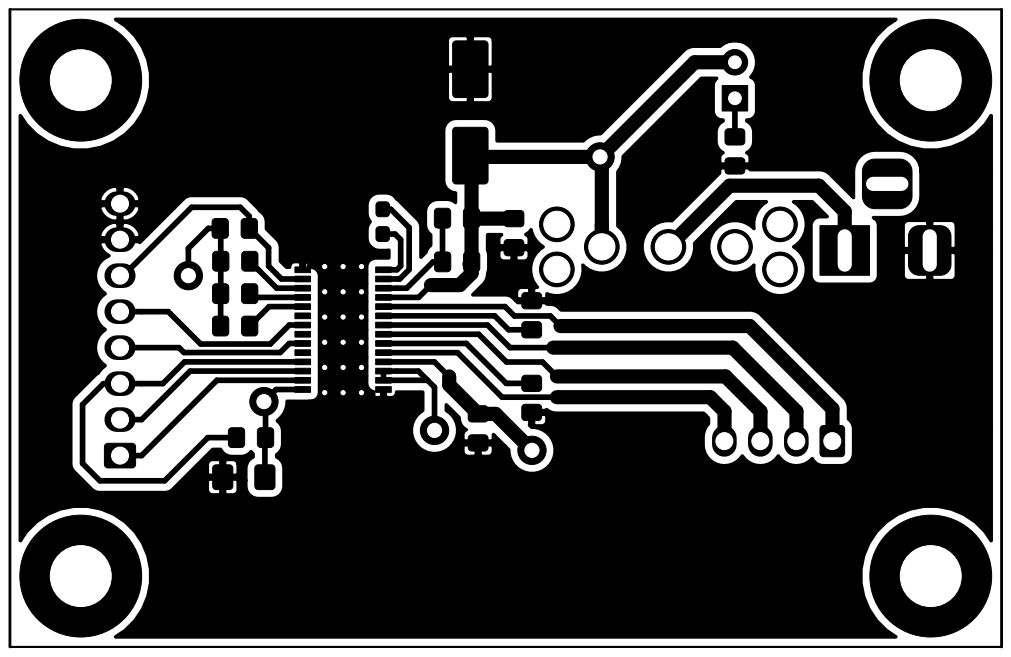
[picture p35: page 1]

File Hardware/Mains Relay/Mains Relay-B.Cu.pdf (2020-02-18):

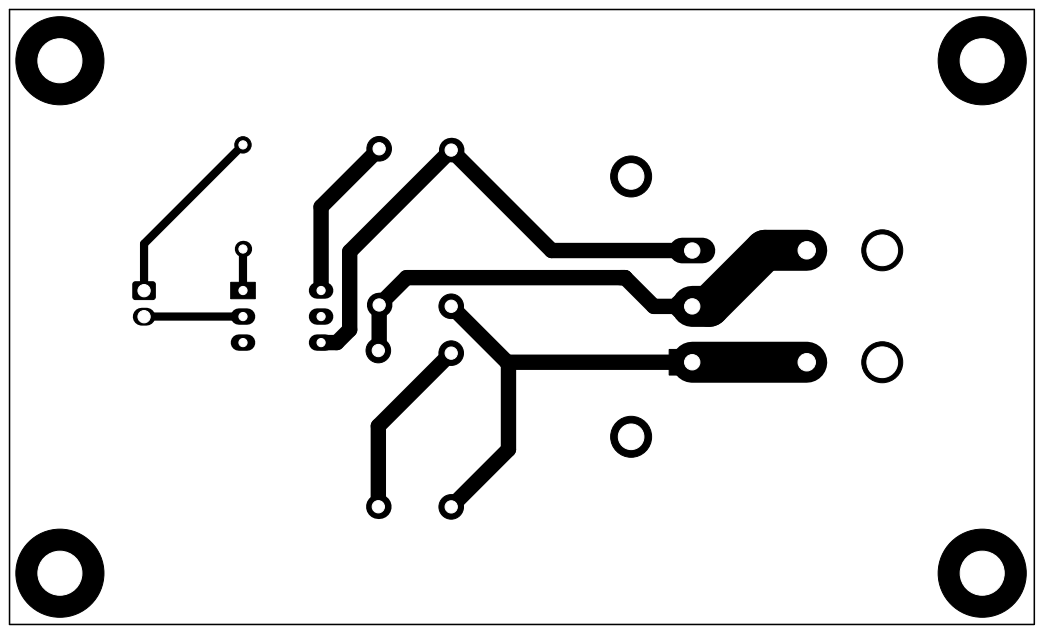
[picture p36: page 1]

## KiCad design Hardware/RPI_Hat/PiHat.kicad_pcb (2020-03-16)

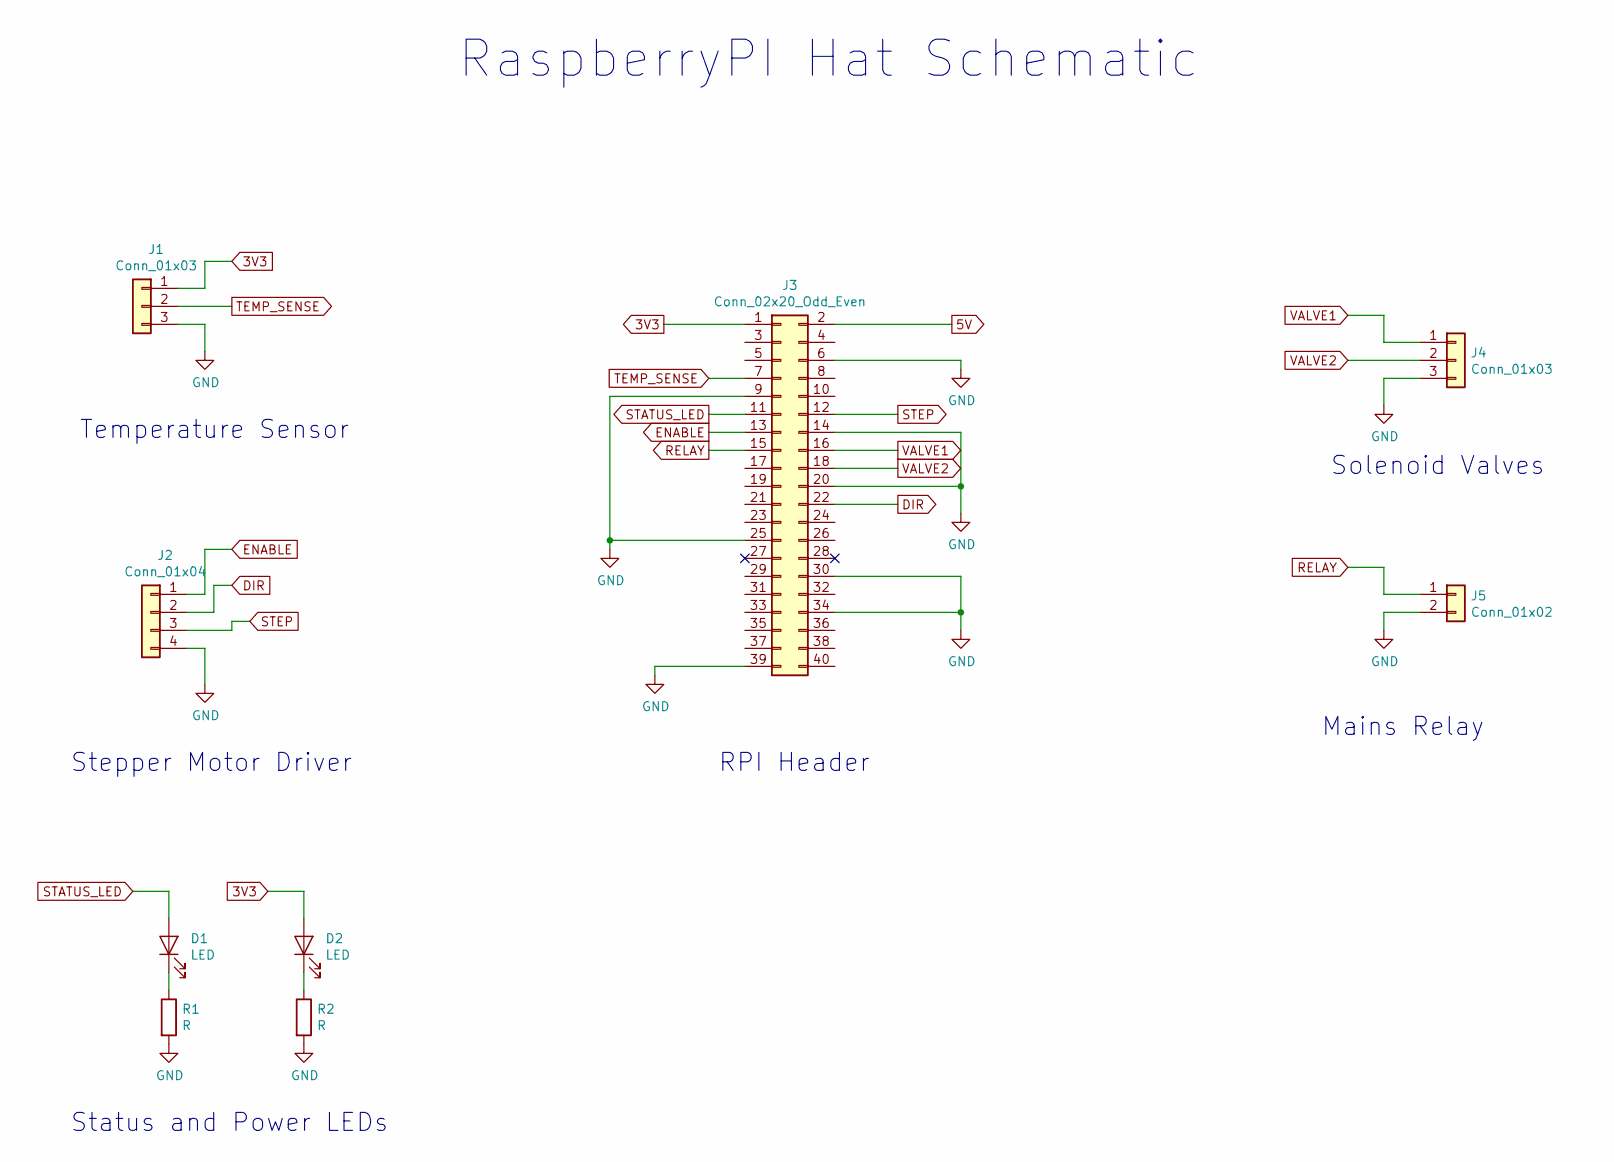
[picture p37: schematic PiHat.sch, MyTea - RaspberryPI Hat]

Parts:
D1, D2: LED; LED_D3.0mm
J1, J4: Conn_01x03; Molex_KK-254_AE-6410-03A_1x03_P2.54mm_Vertical
J2: Conn_01x04; Molex_KK-254_AE-6410-04A_1x04_P2.54mm_Vertical
J3: Conn_02x20_Odd_Even; PinSocket_2x20_P2.54mm_Vertical
J5: Conn_01x02; Molex_KK-254_AE-6410-02A_1x02_P2.54mm_Vertical
R1, R2: R; R_0805_2012Metric_Pad1.15x1.40mm_HandSolder

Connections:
3V3: D2.2 (A), J1.1, J3.1
5V: J3.2
DIR: J2.2, J3.22
ENABLE: J2.1, J3.13
GND: J1.3, J2.4, J3.6, J3.9, J3.14, J3.20, J3.25, J3.30, J3.34, J3.39, J4.3, J5.2, R1.2, R2.2
unnamed: D1.1 (K), R1.1
unnamed: D2.1 (K), R2.1
RELAY: J3.15, J5.1
STATUS_LED: D1.2 (A), J3.11
STEP: J2.3, J3.12
TEMP_SENSE: J1.2, J3.7
VALVE1: J3.16, J4.1
VALVE2: J3.18, J4.2

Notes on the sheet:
RaspberryPI Hat Schematic
Temperature Sensor
Stepper Motor Driver
Solenoid Valves
Mains Relay
Status and Power LEDs
RPI Header

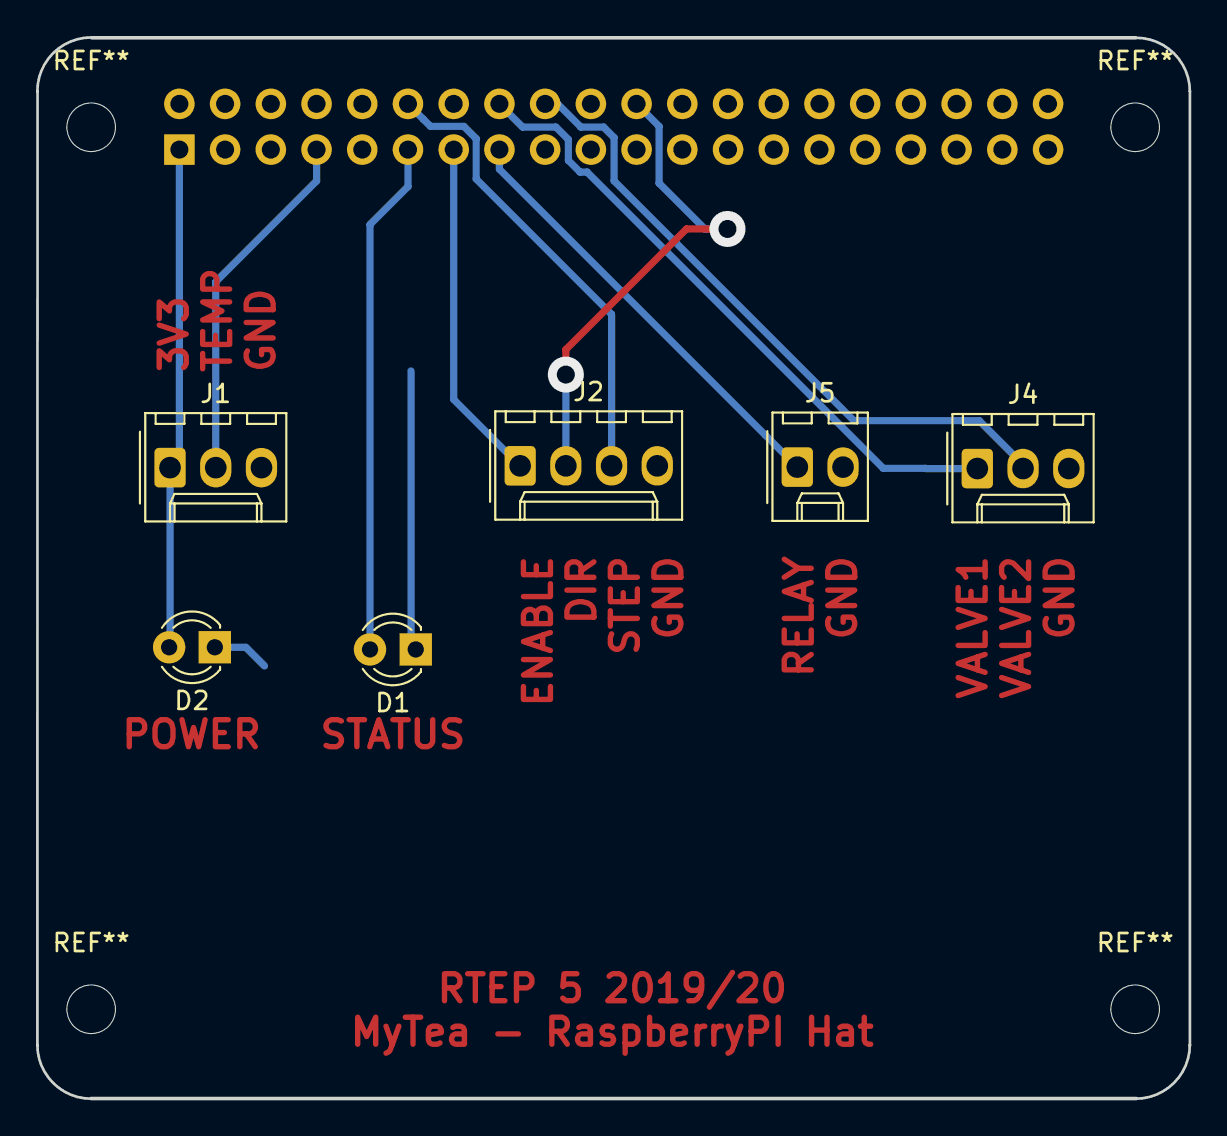
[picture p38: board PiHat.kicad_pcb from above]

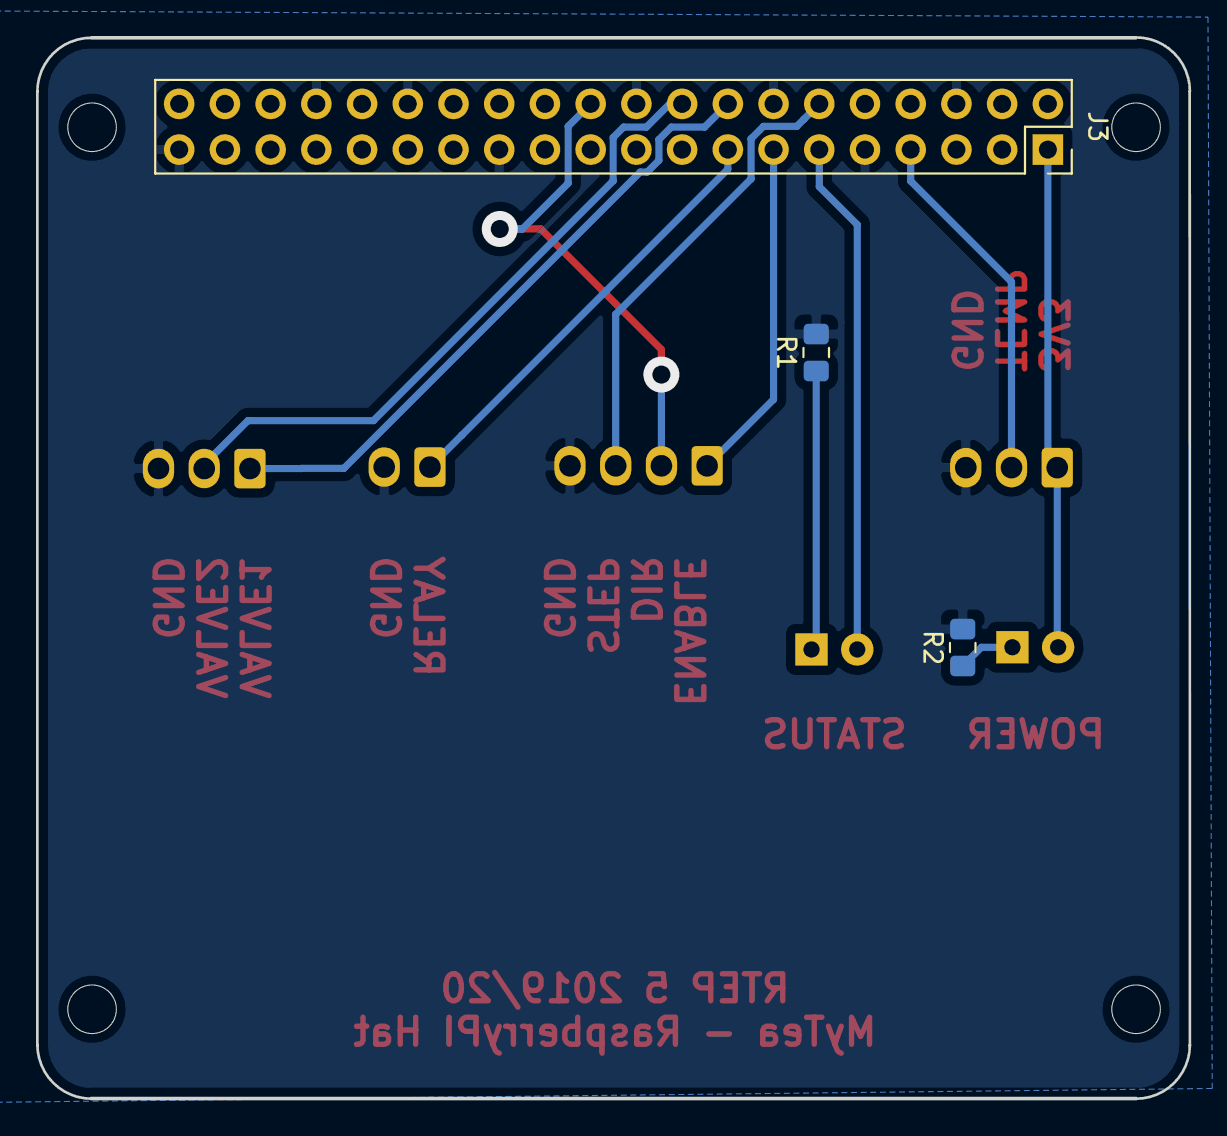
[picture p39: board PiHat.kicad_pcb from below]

Board: 2 copper layers, 64.0 x 59.0 mm, 9 parts (3 on the bottom side), 12 nets.

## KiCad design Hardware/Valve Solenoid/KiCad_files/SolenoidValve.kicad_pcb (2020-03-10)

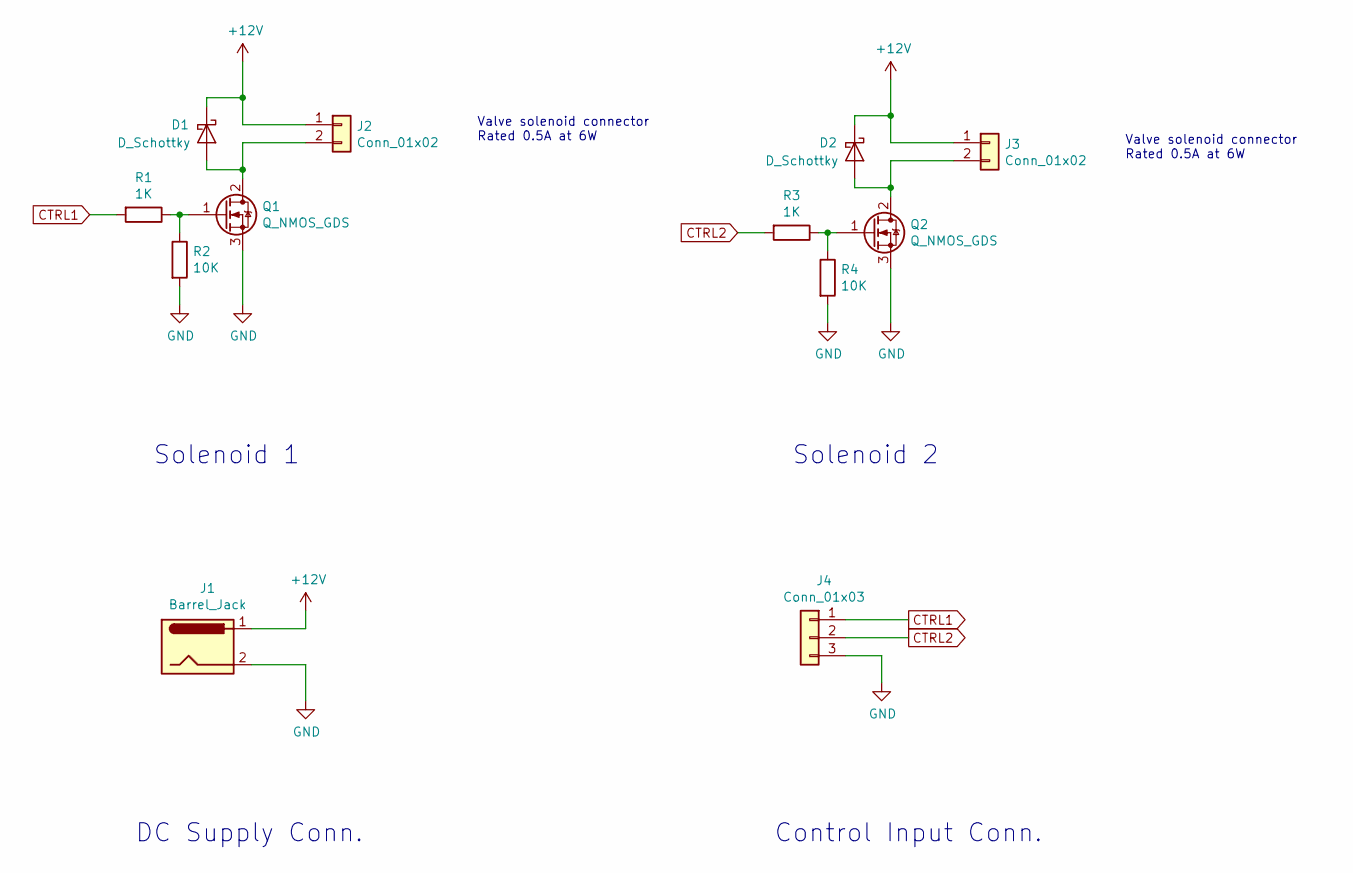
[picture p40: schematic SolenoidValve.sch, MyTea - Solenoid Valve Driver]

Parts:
D1, D2: D_Schottky; D_DO-201AD_P12.70mm_Horizontal
J1: Barrel_Jack; BarrelJack_Horizontal
J2, J3: Conn_01x02; TerminalBlock_Phoenix_PT-1,5-2-5.0-H_1x02_P5.00mm_Horizontal
J4: Conn_01x03; Molex_KK-254_AE-6410-03A_1x03_P2.54mm_Vertical
Q1, Q2: Q_NMOS_GDS; TO-220-3_Vertical
R1, R3: 1K; R_Axial_DIN0207_L6.3mm_D2.5mm_P7.62mm_Horizontal
R2, R4: 10K; R_Axial_DIN0207_L6.3mm_D2.5mm_P7.62mm_Horizontal

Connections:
+12V: D1.1 (K), D2.1 (K), J1.1, J2.1, J3.1
CTRL1: J4.1, R1.2
CTRL2: J4.2, R3.2
GND: J1.2, J4.3, Q1.3 (S), Q2.3 (S), R2.2, R4.2
unnamed: D1.2 (A), J2.2, Q1.2 (D)
unnamed: D2.2 (A), J3.2, Q2.2 (D)
unnamed: Q1.1 (G), R1.1, R2.1
unnamed: Q2.1 (G), R3.1, R4.1

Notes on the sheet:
Valve solenoid connector Rated 0.5A at 6W
Solenoid 1
Solenoid 2
DC Supply Conn.
Control Input Conn.

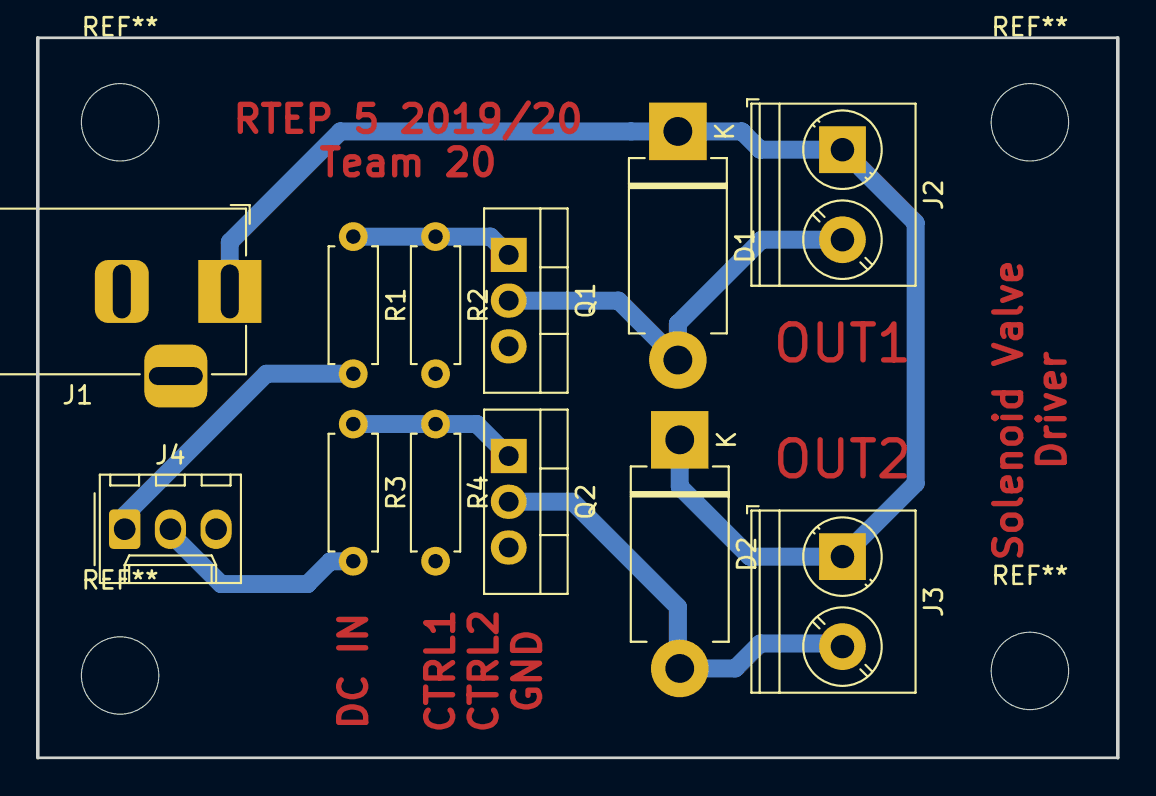
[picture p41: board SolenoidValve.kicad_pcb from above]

Board: 2 copper layers, 60.0 x 40.0 mm, 12 parts (0 on the bottom side), 8 nets.

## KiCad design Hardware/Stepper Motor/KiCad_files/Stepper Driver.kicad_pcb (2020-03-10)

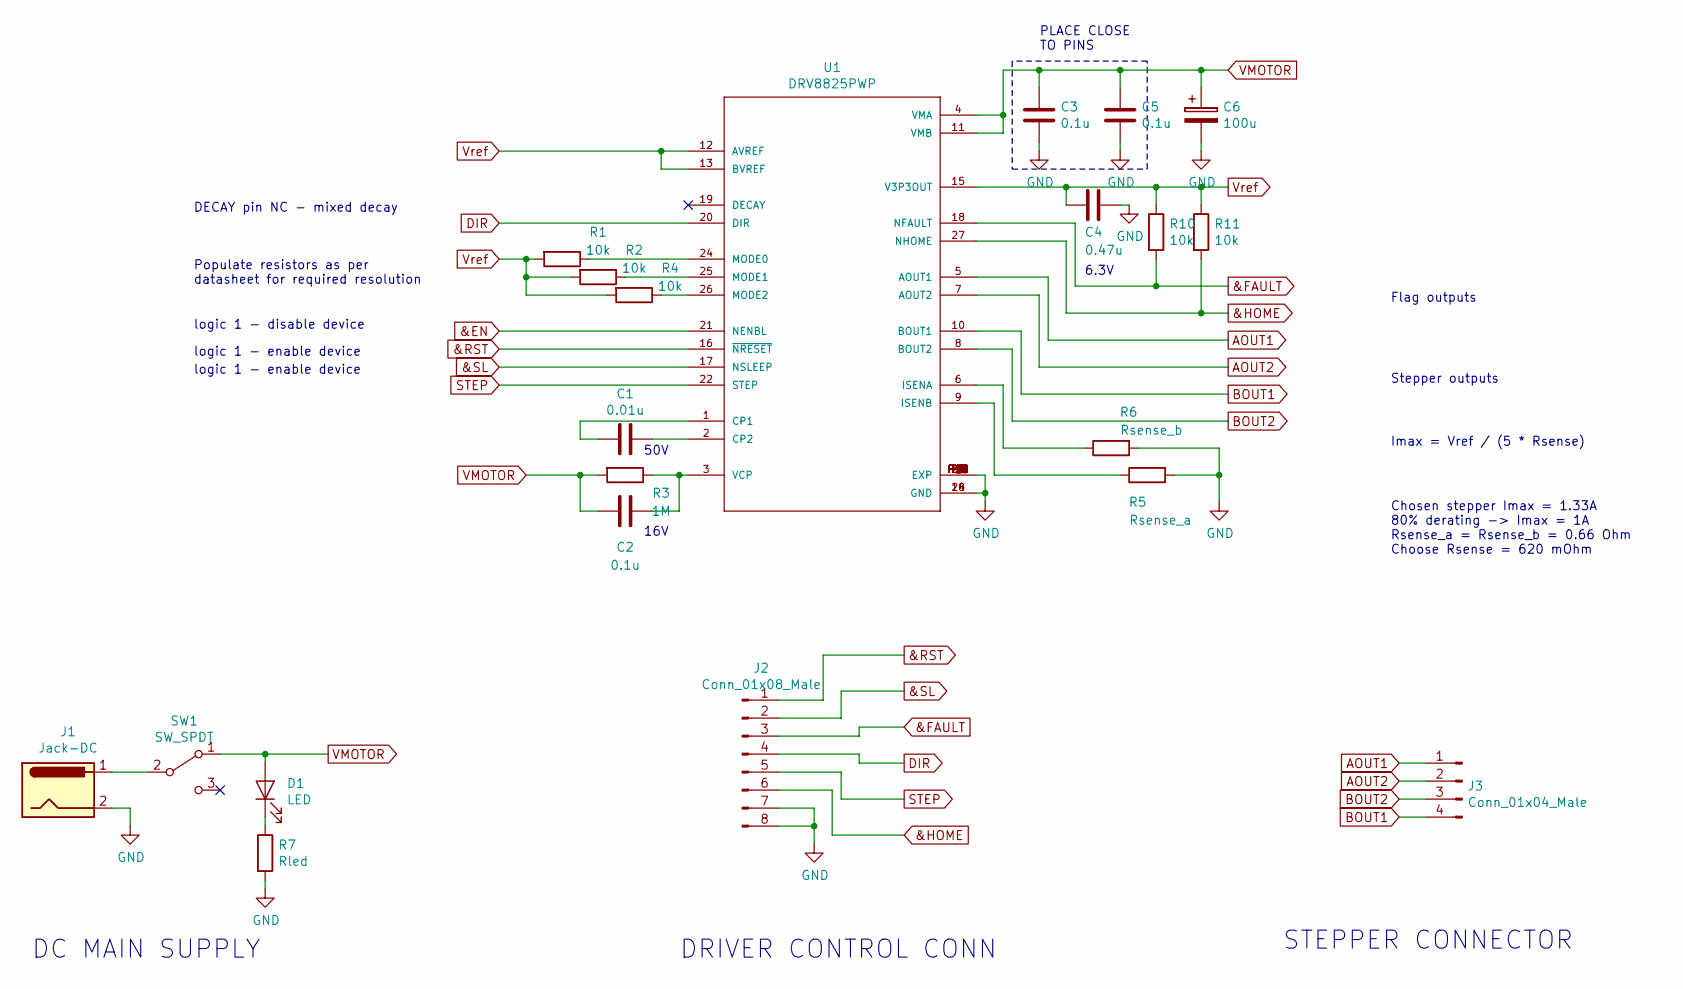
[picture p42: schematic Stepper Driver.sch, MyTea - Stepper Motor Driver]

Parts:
C1: 0.01u; C_0603_1608Metric_Pad1.05x0.95mm_HandSolder
C2, C3, C5: 0.1u; C_0805_2012Metric_Pad1.15x1.40mm_HandSolder
C4: 0.47u; C_1206_3216Metric_Pad1.42x1.75mm_HandSolder
C6: 100u; CP_Elec_8x5.4
D1: LED; LED_D3.0mm
J1: Jack-DC; BarrelJack_Horizontal
J2: Conn_01x08_Male; Molex_KK-254_AE-6410-08A_1x08_P2.54mm_Vertical
J3: Conn_01x04_Male; Molex_KK-254_AE-6410-04A_1x04_P2.54mm_Vertical
R1, R2, R4, R10, R11: 10k; R_0805_2012Metric_Pad1.15x1.40mm_HandSolder
R3: 1M; R_0805_2012Metric_Pad1.15x1.40mm_HandSolder
R5: Rsense_a; R_0805_2012Metric_Pad1.15x1.40mm_HandSolder
R6: Rsense_b; R_0805_2012Metric_Pad1.15x1.40mm_HandSolder
R7: Rled; R_0805_2012Metric_Pad1.15x1.40mm_HandSolder
SW1: SW_SPDT; SPDT_RockerSwitch
U1: DRV8825PWP; HTSSOP-28-1EP_4.4x9.7mm_P0.65mm_EP3.4x9.5mm_Mask2.4x6.17mm_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

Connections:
&EN: U1.21 (NENBL)
&FAULT: J2.3, R10.2, U1.18 (NFAULT)
&HOME: J2.6, R11.2, U1.27 (NHOME)
&RST: J2.1, U1.16 (~NRESET~)
&SL: J2.2, U1.17 (NSLEEP)
AOUT1: J3.1, U1.5 (AOUT1)
AOUT2: J3.2, U1.7 (AOUT2)
BOUT1: J3.4, U1.10 (BOUT1)
BOUT2: J3.3, U1.8 (BOUT2)
DIR: J2.4, U1.20 (DIR)
GND: C3.1, C4.1, C5.1, C6.2, J1.2, J2.7, J2.8, R5.2, R6.2, R7.2, U1.14 (GND), U1.28 (GND), U1.29 (EXP), U1.P1 (EXP), U1.P2 (EXP), U1.P3 (EXP), U1.P4 (EXP), U1.P5 (EXP), U1.P6 (EXP), U1.P7 (EXP), U1.P8 (EXP), U1.P9 (EXP), U1.P10 (EXP), U1.P11 (EXP), U1.P12 (EXP), U1.P13 (EXP), U1.P14 (EXP), U1.P15 (EXP), U1.P16 (EXP), U1.P17 (EXP), U1.P18 (EXP), U1.P19 (EXP), U1.P20 (EXP), U1.P21 (EXP), U1.P22 (EXP), U1.P23 (EXP), U1.P24 (EXP)
unnamed: C1.1, U1.1 (CP1)
unnamed: C1.2, U1.2 (CP2)
unnamed: C2.2, R3.1, U1.3 (VCP)
unnamed: D1.1 (K), R7.1
unnamed: J1.1, SW1.2 (B)
unnamed: R1.1, U1.24 (MODE0)
unnamed: R2.1, U1.25 (MODE1)
unnamed: R4.1, U1.26 (MODE2)
unnamed: R5.1, U1.9 (ISENB)
unnamed: R6.1, U1.6 (ISENA)
STEP: J2.5, U1.22 (STEP)
VMOTOR: C2.1, C3.2, C5.2, C6.1, D1.2 (A), R3.2, SW1.1 (A), U1.4 (VMA), U1.11 (VMB)
Vref: C4.2, R1.2, R2.2, R4.2, R10.1, R11.1, U1.12 (AVREF), U1.13 (BVREF), U1.15 (V3P3OUT)

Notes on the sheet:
50V
PLACE CLOSE TO PINS
16V
6.3V
STEPPER CONNECTOR
Imax = Vref / (5 * Rsense)
Chosen stepper Imax = 1.33A 80% derating -> Imax = 1A Rsense_a = Rsense_b = 0.66 Ohm Choose Rsense = 620 mOhm
DC MAIN SUPPLY
Populate resistors as per datasheet for required resolution
DRIVER CONTROL CONN
Flag outputs
Stepper outputs
DECAY pin NC - mixed decay
logic 1 - disable device
logic 1 - enable device

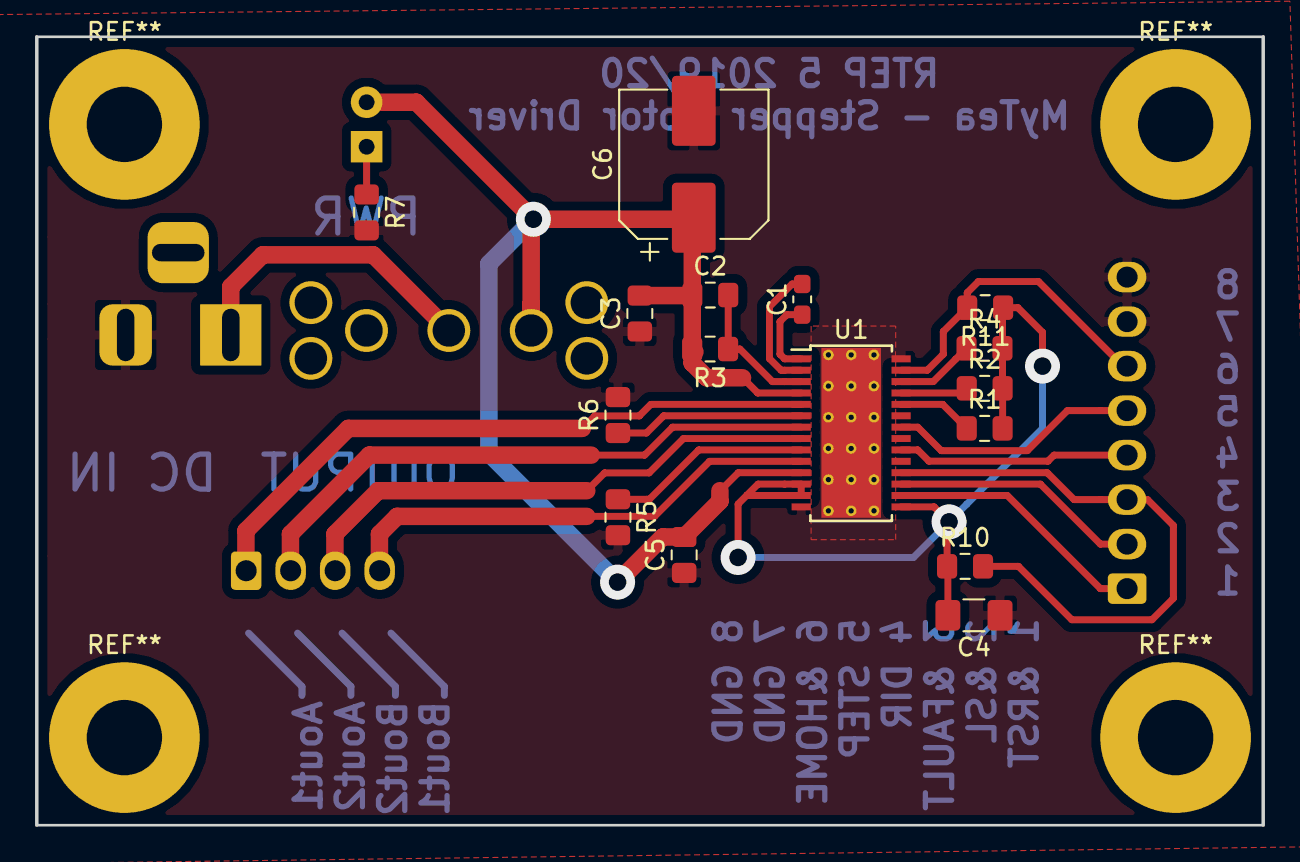
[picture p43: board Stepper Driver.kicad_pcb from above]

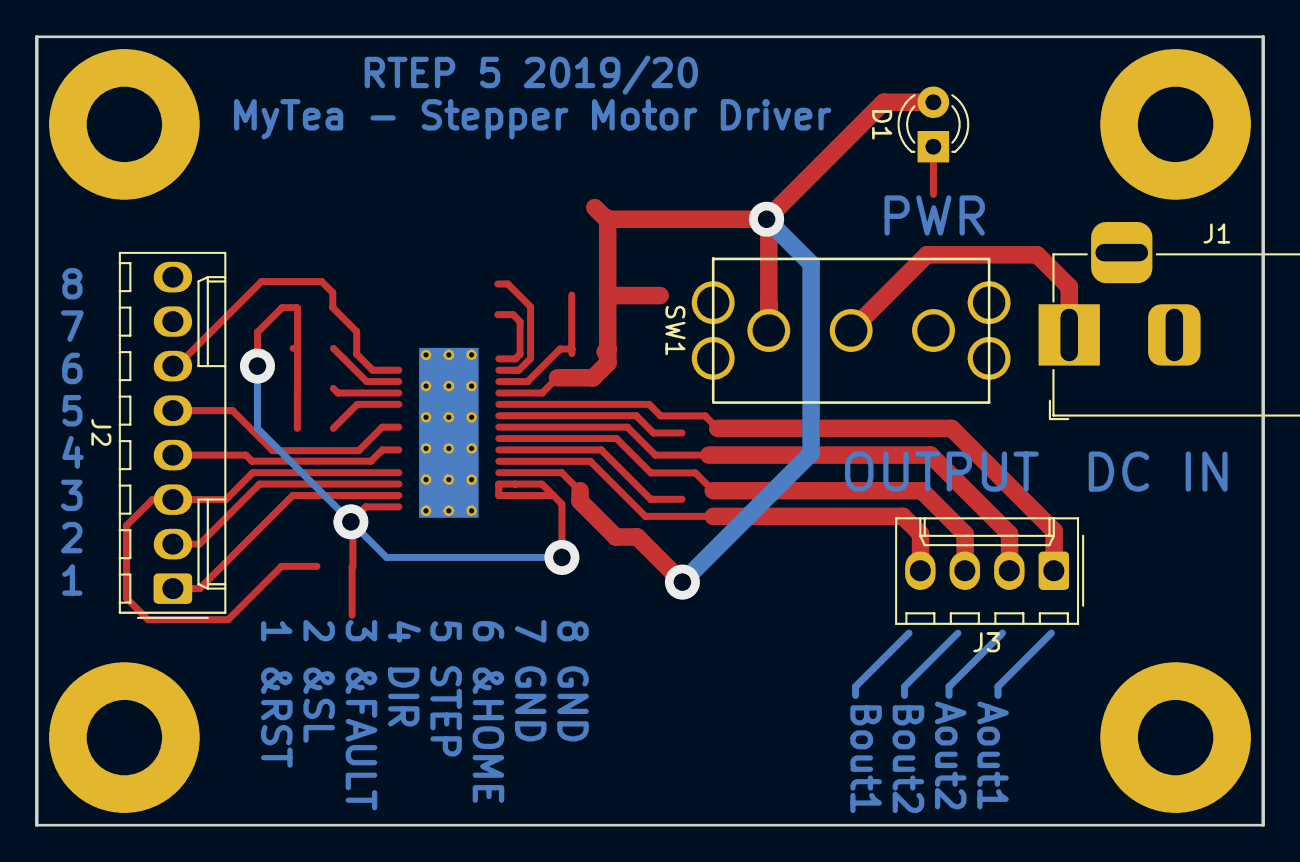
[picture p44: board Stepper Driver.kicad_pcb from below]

Board: 2 copper layers, 70.0 x 45.0 mm, 21 parts (5 on the bottom side), 23 nets.

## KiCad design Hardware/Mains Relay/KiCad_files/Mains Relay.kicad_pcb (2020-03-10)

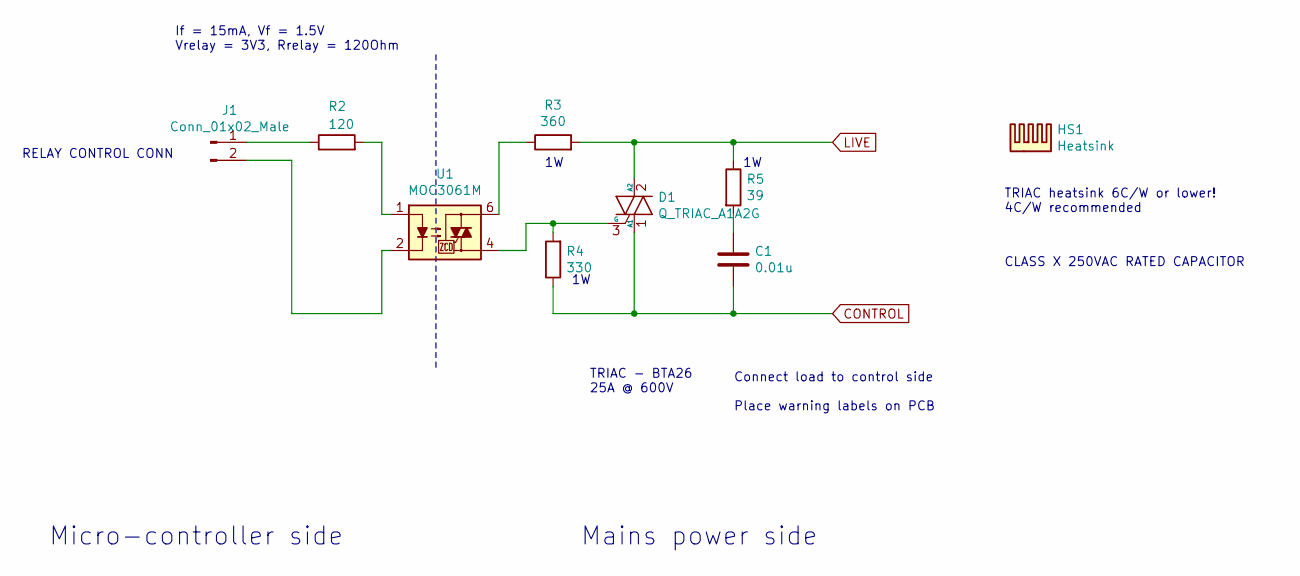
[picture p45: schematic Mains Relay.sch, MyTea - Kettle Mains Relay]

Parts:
C1: 0.01u; C_Rect_L18.0mm_W5.0mm_P15.00mm_FKS3_FKP3
D1: Q_TRIAC_A1A2G; TO-3P-3_Vertical
HS1: Heatsink; Heatsink_Fischer_SK129-STS_42x25mm_2xDrill2.5mm
J1: Conn_01x02_Male; Molex_KK-254_AE-6410-02A_1x02_P2.54mm_Vertical
R2: 120; R_Axial_DIN0207_L6.3mm_D2.5mm_P10.16mm_Horizontal
R3: 360; R_Axial_DIN0414_L11.9mm_D4.5mm_P15.24mm_Horizontal
R4: 330; R_Axial_DIN0414_L11.9mm_D4.5mm_P15.24mm_Horizontal
R5: 39; R_Axial_DIN0414_L11.9mm_D4.5mm_P15.24mm_Horizontal
U1: MOC3061M; DIP-6_W7.62mm_Socket_LongPads

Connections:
CONTROL: C1.2, D1.1 (A1), R4.1
LIVE: D1.2 (A2), R3.2, R5.1
unnamed: C1.1, R5.2
unnamed: D1.3 (G), R4.2, U1.4
unnamed: J1.1, R2.1
unnamed: J1.2, U1.2
unnamed: R2.2, U1.1
unnamed: R3.1, U1.6

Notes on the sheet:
If = 15mA, Vf = 1.5V Vrelay = 3V3, Rrelay = 120Ohm
RELAY CONTROL CONN
TRIAC heatsink 6C/W or lower! 4C/W recommended
Micro-controller side
TRIAC - BTA26 25A @ 600V
Mains power side
Connect load to control side Place warning labels on PCB
CLASS X 250VAC RATED CAPACITOR

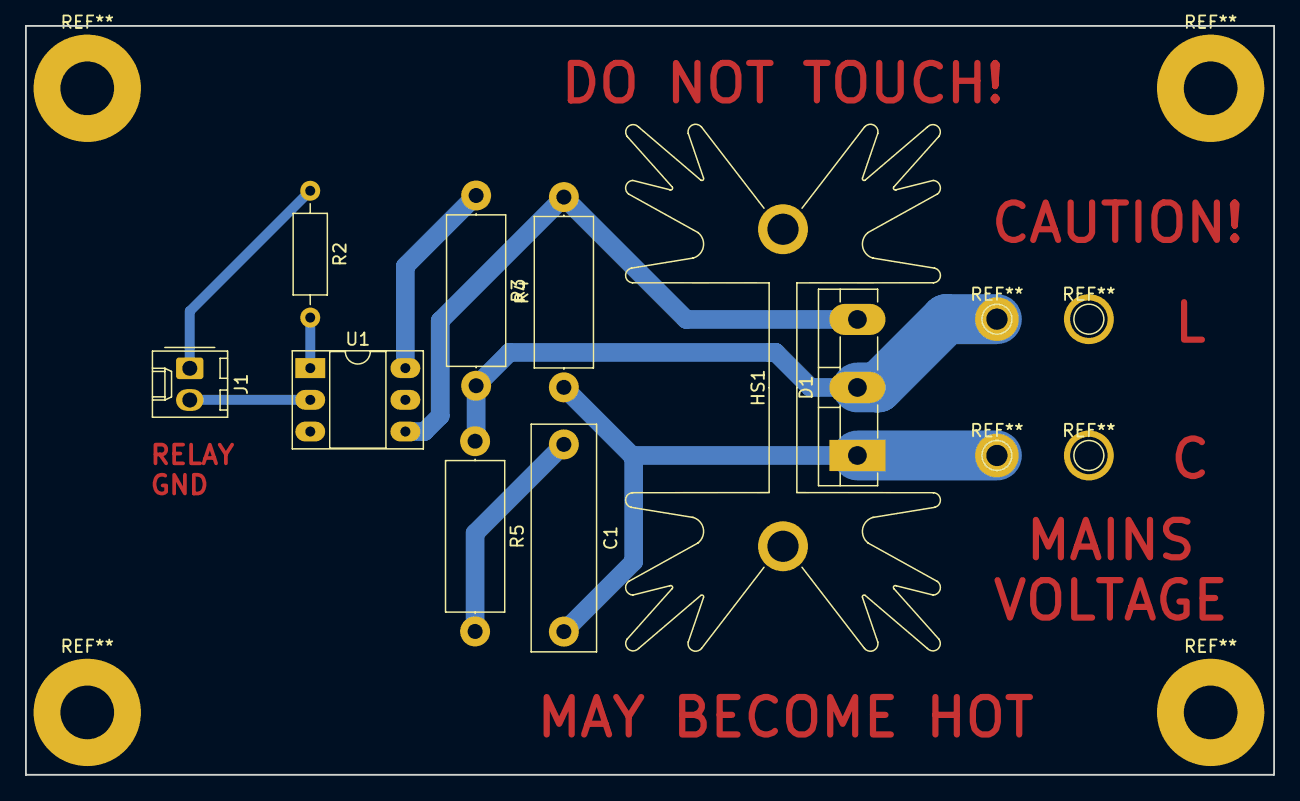
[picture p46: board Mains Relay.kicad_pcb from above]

Board: 2 copper layers, 100.0 x 60.0 mm, 9 parts (0 on the bottom side), 8 nets.

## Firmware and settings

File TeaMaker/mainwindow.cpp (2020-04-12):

#include "mainwindow.h"
#include "ui_mainwindow.h"

#include <stdio.h>
#include <unistd.h>
#include <time.h>
#include <thread>
#include "header/CppTimer.h"
#include "header/CppThread.h"
#include "header/RealTime_Sensor.h"
#include "header/RealTime_Switch.h"
#include "header/RealTime_Motor.h"
#include "wiringPi.h"

MainWindow::MainWindow(QWidget *parent)
    : QMainWindow(parent)
    , ui(new Ui::MainWindow)
{
    ui->setupUi(this);

    wiringPiSetup ();
    pinMode (3, OUTPUT) ;     // relay
    pinMode (4, OUTPUT) ;     // valve 1
    pinMode (5, OUTPUT) ;	  // valve 2

}

MainWindow::~MainWindow()
{
    delete ui;
}



void MainWindow::on_GreenTea_clicked()
{

    // temperature = 80 degrees
    // amount of water = 200 ml
    // amount of tea leaves = 5 g
    // tea brew time = 2 min

    float target = 30000;

    // Turn on the heater
    Relay relay;
    relay.on();

    // Dispense tea leaves in a thread
    Motor motor(1, 27, 60);
    motor.init();
    motor.start();
    motor.join();

    // Sensor reading
    Sensor sensor;
    sensor.LEDon();
    sensor.init();
    sensor.check();

    sensor.start(2000000000, PERIODIC);

    while (1) {
    std::this_thread::sleep_for(std::chrono::seconds(1));

    if (sensor.getTemp() > target){
        break;
      }
    }

    sensor.stop();
    sensor.LEDoff();

    // Turn off the heater
    relay.start(100000000, ONESHOT);
    std::this_thread::sleep_for(std::chrono::seconds(2));

    // Open valve 1
    Valve1 valve1;
    valve1.on();

    // Close Valve 2
    valve1.start(100000000, ONESHOT);
    std::this_thread::sleep_for(std::chrono::seconds(2));

    // Tea brew time for 2 min
    fprintf(stdout,"Tea brew time ...\n");
    std::this_thread::sleep_for(std::chrono::minutes(1));

    // Open valve 2
    Valve2 valve2;
    valve2.on();

    // Close valve 2
    valve2.start(100000000, ONESHOT);
    std::this_thread::sleep_for(std::chrono::seconds(2));
}


void MainWindow::on_BlackTea_clicked()
{

    // temperature = 100 degrees
    // amount of water = 200 ml
    // amount of tea leaves = 5 g
    // tea brew time = 3 min

    float target = 30000;

    // Turn on the heater
    Relay relay;
    relay.on();

    // Dispense tea leaves in a thread
    Motor motor(1, 27, 60);
    motor.init();
    motor.start();
    motor.join();

    // Sensor reading
    Sensor sensor;
    sensor.LEDon();
    sensor.init();
    sensor.check();
    sensor.start(2000000000, PERIODIC);

    while (1) {
    std::this_thread::sleep_for(std::chrono::seconds(1));

    if (sensor.getTemp() > target){
        break;
      }
    }

    sensor.stop();
    sensor.LEDoff();

    // Turn off the heater
    relay.start(100000000, ONESHOT);
    std::this_thread::sleep_for(std::chrono::seconds(2));

    // Open valve 1
    Valve1 valve1;
    valve1.on();

    // Close Valve 2
    valve1.start(100000000, ONESHOT);
    std::this_thread::sleep_for(std::chrono::seconds(2));

    // Tea brew time for 2 min
    fprintf(stdout,"Tea brew time ...\n");
    std::this_thread::sleep_for(std::chrono::minutes(1));

    // Open valve 2
    Valve2 valve2;
    valve2.on();

    // Close valve 2
    valve2.start(100000000, ONESHOT);
    std::this_thread::sleep_for(std::chrono::seconds(2));
}

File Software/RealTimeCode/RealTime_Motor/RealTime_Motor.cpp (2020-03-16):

#include <stdio.h>
#include <stdlib.h>
#include <unistd.h>
#include <wiringPi.h>
#include <chrono>
#include <stdio.h>
#include <thread>
#include <chrono>
#include "RealTime_Motor.h"

void Motor::init(){
  wiringPiSetup ();
  pinMode (STEP, OUTPUT);
  pinMode (CHIPEN, OUTPUT);
  pinMode (DIR, OUTPUT);
 }

void Motor:: run(){
  
  printf("Running in a thread\n");

  digitalWrite (CHIPEN, HIGH);
  digitalWrite (DIR, clockwise);
  int stepperPeriod = 200 / speed;
  int pulses = degrees / 0.9;
  std::this_thread::sleep_for(std::chrono::milliseconds(5));
  for(int i = 0; i < pulses; i++){
    digitalWrite (STEP, HIGH);
    std::this_thread::sleep_for(std::chrono::milliseconds(stepperPeriod/2));
    digitalWrite (STEP, LOW);
    std::this_thread::sleep_for(std::chrono::milliseconds(stepperPeriod/2));
    }
  
  std::this_thread::sleep_for(std::chrono::milliseconds(500));    
  digitalWrite (DIR, !clockwise);
  
  for(int i = 0; i < pulses; i++){
    digitalWrite (STEP, HIGH);
    std::this_thread::sleep_for(std::chrono::milliseconds(stepperPeriod/2));
    digitalWrite (STEP, LOW);
    std::this_thread::sleep_for(std::chrono::milliseconds(stepperPeriod/2));
  }
  }

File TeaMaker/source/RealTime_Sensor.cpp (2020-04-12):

#include <stdio.h>
#include <dirent.h>
#include <string.h>
#include <fcntl.h>
#include <stdlib.h>
#include <unistd.h>
#include <wiringPi.h>
#include "header/RealTime_Sensor.h"
#include "header/CppTimer_sensor.h"

DIR *dir;
struct dirent *dirent;
char dev[16];      // Dev ID
char devPath[128]; // Path to device
char buf[256];     // Data from device
char tmpData[6];   // Temp C * 1000 reported by device
char path[] = "/sys/bus/w1/devices";

int fd;
	
ssize_t numRead;


// Constructor 
Sensor::Sensor(){}

void Sensor::init(){
	wiringPiSetup ();
	pinMode (LED, OUTPUT) ;
 }
  
float Sensor::getTemp(){
  return tempC;
  }
  
  
   void Sensor::check(){
	   
	 dir = opendir (path);
	 
	 if (dir != NULL){
		  while ((dirent = readdir (dir)))
		   // 1-wire devices are links beginning with 28-
		   if (dirent->d_type == DT_LNK && strstr(dirent->d_name, "28-") != NULL) {
				strcpy(dev, dirent->d_name);
				printf("\nDevice: %s\n", dev);
		   }
				(void) closedir (dir);
		}
		
	 else {
		  perror ("Couldn't open the w1 devices directory");
		}

	 // Assemble path to OneWire device
	 sprintf(devPath, "%s/%s/w1_slave", path, dev);
	}
  
  
   void Sensor::timerEvent(){
	 
	 // Read temp continuously
	 
	  int fd = open(devPath, O_RDONLY);
	  
	  if(fd == -1){
		   perror ("Couldn't open the w1 device.");
	  }
	  
	  if((numRead = read(fd, buf, 256)) > 0){
		   strncpy(tmpData, strstr(buf, "t=") + 2, 5);
		   tempC = strtof(tmpData, NULL);
		   printf("Device: %s  - ", dev);
		   printf("Temp: %.3f C  ", tempC / 1000);
		   printf("%.3f F\n\n", (tempC / 1000) * 9 / 5 + 32);
		  
		}
		
	  close(fd);
    }
  
  
  
  void Sensor::blinkLED(){
	  printf ("Raspberry Pi blink\n") ;
  
      for (;;){
		digitalWrite (LED, HIGH) ;	// On
		delay (500) ;		        // mS
		digitalWrite (LED, LOW) ;	// Off
		delay (500) ;
	  }
  }

  void Sensor::LEDon(){
      digitalWrite (LED, HIGH) ;	// On
  }

  void Sensor::LEDoff(){
      digitalWrite (LED, LOW) ;	// On
  }

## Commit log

2020-01-26 Initial pitch presentation added
2020-02-18 Created mains relay verification procedure
2020-02-18 Added functional testing scope traces
2020-02-18 Added schematic and layer masks
2020-02-18 sample code for blinking LED
2020-02-20 Uploaded stepper motor driver masks
2020-02-20 Uploaded solenoid valve layer masks
2020-02-24 Uploaded stepper driver schematic
2020-02-24 Uploaded stepper driver interactive BOM
2020-02-24 Uploaded stepper driver BOM
2020-02-26 Fixed LED not blinking
2020-02-26 Stepper motor test code initial release
2020-03-03 Motor test code done
2020-03-03 Sensor test code done
2020-03-03 Switch test code done
2020-03-09 Real_time sensor
2020-03-10 Create README for mains relay
2020-03-10 Added KiCad files for mains relay
    [Mains Relay.kicad_pcb, Mains Relay.sch]
2020-03-10 Add KiCad files
    [Stepper Driver.kicad_pcb, Stepper Driver.sch]
2020-03-10 Add KiCad files for solenoid valve
    [SolenoidValve.kicad_pcb, SolenoidValve.sch]
2020-03-10 Add mechanical drawing for enclosure
2020-03-10 Motor runs in a thread
2020-03-11 Switch is implemented in real time
2020-03-11 Add SOLIDWORKS models
    [BottomPlate13mm.SLDPRT, BottomPlate15mm.SLDPRT, BottomPlateRot.SLDPRT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]
2020-03-12 Real Time sensor was implemented in .h and .cpp files
2020-03-12 Real Time motor is implemented with cppThread
2020-03-12 motor test done
2020-03-12 fixed bug in Real Time switch
    [RealTime_Switch_test.cpp]
2020-03-13 Real Time Sensor is implemented
2020-03-16 Add KiCad files for RPI hat
    [PiHat.kicad_pcb, PiHat.sch]
2020-03-16 motor rotation became bidirectional
2020-03-16 initial Qt with relay switch
2020-03-16 fixed links between source files
    [RealTime_Switch.cpp, mainwindow.cpp]
2020-03-19 Real Time Switch 2 file was modified
2020-03-19 Real Time Switch 2 repository is cleaned up
2020-04-12 All switches were implememted
2020-04-12 A bug was fixed
    [RealTime_Switch.cpp]
2020-04-12 Sensor was implemnted in Qt
2020-04-12 modified LED function in Sensor
2020-04-12 Motor is implemnted in Qt
2020-04-12 Add pitch presentation
2020-04-13 Add mains relay BoM
2020-04-13 Add mains relay interactive BoM
2020-04-13 Add solenoid valve schem and BoM
2020-04-13 Add valve solenoid interactive BoM
2020-04-13 Add PI hat BoM and interactive BoM
2020-04-13 Add PI hat PCB layer masks
2020-04-13 Add stepper driver image
2020-04-13 Add assembly drawing
2020-04-13 Add assembly models
    [BasePlate.SLDPRT, Container.SLDPRT, Fitting.SLDPRT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]
2020-04-14 Add PI hat schematic
2020-04-16 changed name to docs
    [BasePlate.SLDPRT, BottomPlate13mm.SLDPRT, BottomPlate15mm.SLDPRT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]
2020-04-16 deleted docs/
    [BasePlate.SLDPRT, BottomPlate13mm.SLDPRT, BottomPlate15mm.SLDPRT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]
